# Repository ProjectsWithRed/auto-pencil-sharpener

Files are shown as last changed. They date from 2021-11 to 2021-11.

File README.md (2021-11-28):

# Automatic pencil sharpener

An automatic pencil sharpener machine that works using linear motion. You can sharpen any pencil just by pressing a button and it will take care of the rest, including gathering up all the rubbish into a container.

There is a [video](https://youtu.be/7P9160cqDPM) associated with this repository/project, I highly recommend watching it before using this repo.

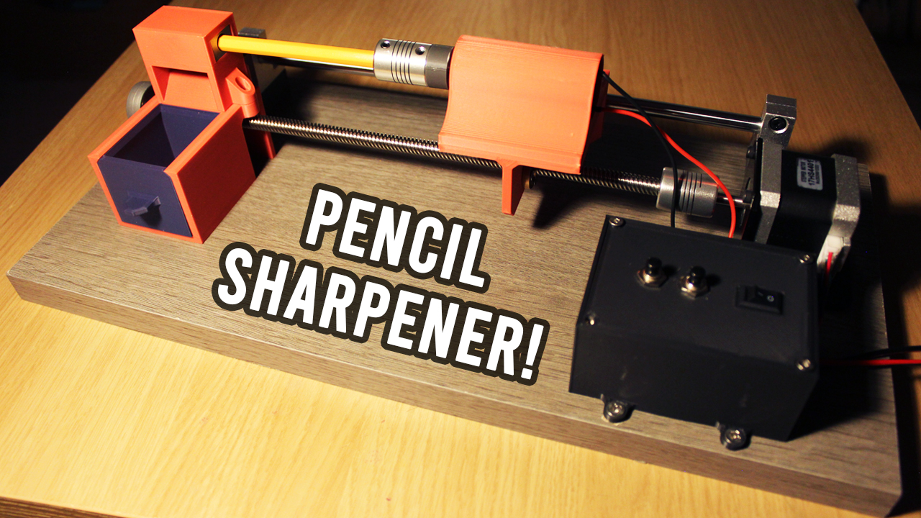
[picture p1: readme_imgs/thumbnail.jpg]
Video (https://youtu.be/7P9160cqDPM "Automatic Pencil Sharpener")


# Arduino

You can find the Arduino sketch in the `auto_pencil_sharpener` directory.

## How to upload code to Attiny MCs if needed

- The Attiny MCs can be programmed just like any Arduino and it's very easy to upload code to them.
- You just need a USBASP adapter, then simply make the connections as shown in the image below.

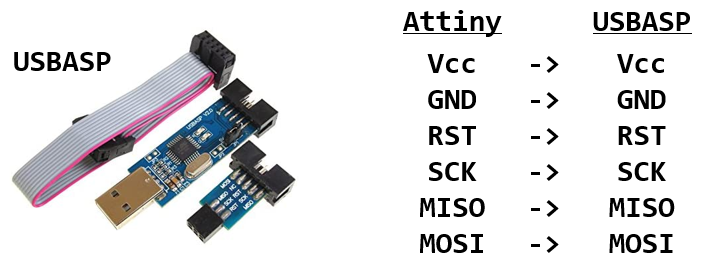
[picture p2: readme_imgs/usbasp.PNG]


- You will also need to install the Attiny boards using the [AttinyCore](https://github.com/SpenceKonde/ATTinyCore) board manager by placing this link `http://drazzy.com/package_drazzy.com_index.json` to your "Additional Boards Manager URLs", which can be accessed in `File > Preferences`.

- From `Tools > Board`, choose your Attiny board with the no bootloader option.
- Then go to `Tools > Programmer` and choose `USBasp (ATTinyCore)`, and then press `Tools > Burn Bootloader`.
- Then to simply upload code, use `Sketch > Upload Using Programmer`.

- You can use stripboards with some wires to make uploading code to the Attiny MCs more convenient:

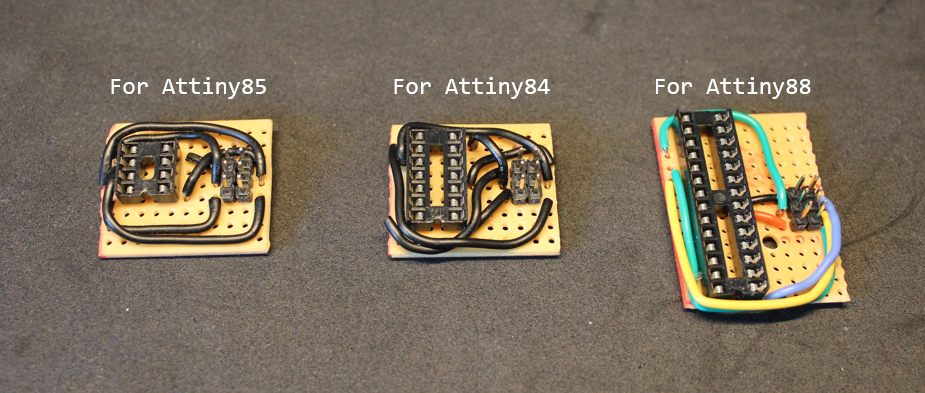
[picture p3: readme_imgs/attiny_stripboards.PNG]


# Components

- `Attiny84`, for the micro-controller.
- `Nema 17` stepper motor, to drive the linear motion.
- `A4988` stepper motor driver, with 100µF-1000µF capacitor across the motor power pins.
- `12V` power supply, with at least 3A max rated current.
- `LM2596` DC-DC step up/down converter, to convert 12V to 5V. 12V is required for the motors, 5V for the micro-controller.
- `MCP1700`, 5V voltage regulator, to ensure the Attiny84 has a consistent and smooth voltage. 1000/100µF and 100,000pF capacitors are soldered directly on the MCP1700 to deal with voltage spikes.
- `12V DC motor`, the one used has a max speed of 500 RPM.
- `IRF3708 MOSFET`, to be able to control the DC motor using a micro-controller.
- `1N4004 Diode`, to be placed across the DC motor to prevent negative voltage spikes if the DC motor is rotated when the circuit is off.
- `Sliding switch`, as an on and off switch.
- `2 buttons`, to control the stepper motor, left and right controls.
- `8mm L30cm lead screw`, for the linear motion.
- `8mm L30cm smooth rod`, for the linear rail for the linear motion.
- `Pillow block bearing`, for the lead screw.
- `SCS8UU linear bearing`, for the smooth rod.
- `SK8 rod support` (x2), for the smooth rod.
- `D19L25 5x8mm flexible shaft coupling` (x2), one to attach lead screw to stepper motor and one to attach pencil to DC motor.

Optional:
- `Potentiometer`, this will be used to fine-tune the speed of the stepper motor, so it does not move too fast towards the sharpener.

# Wiring

## Breadboard

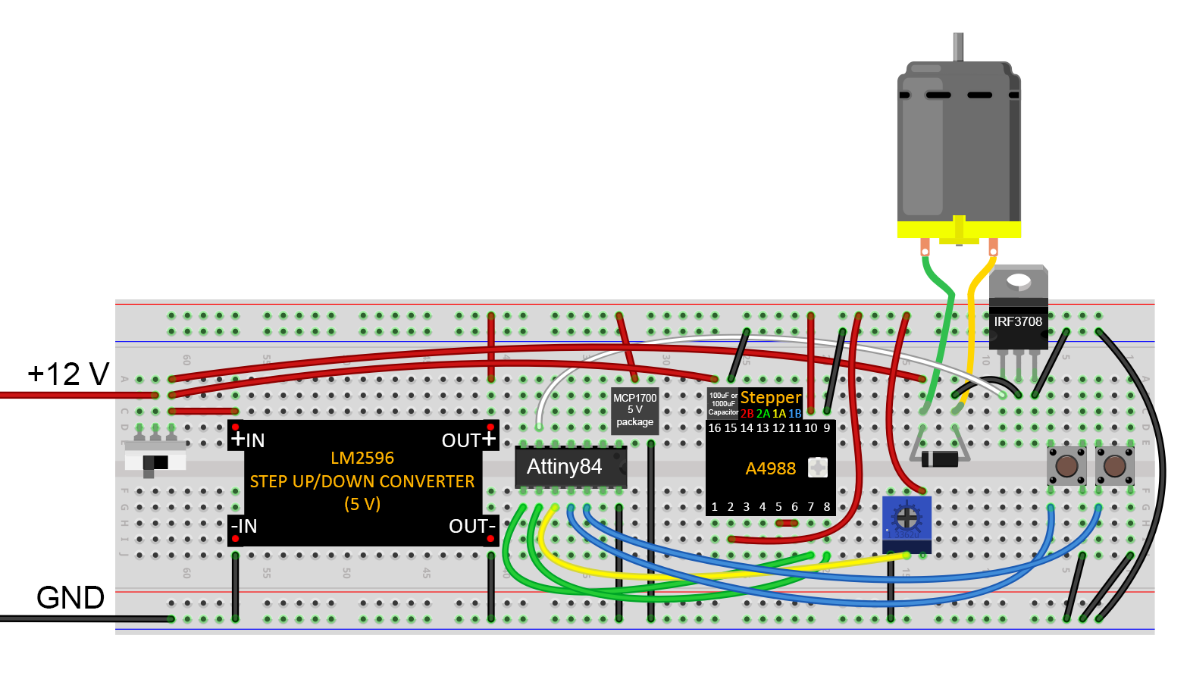
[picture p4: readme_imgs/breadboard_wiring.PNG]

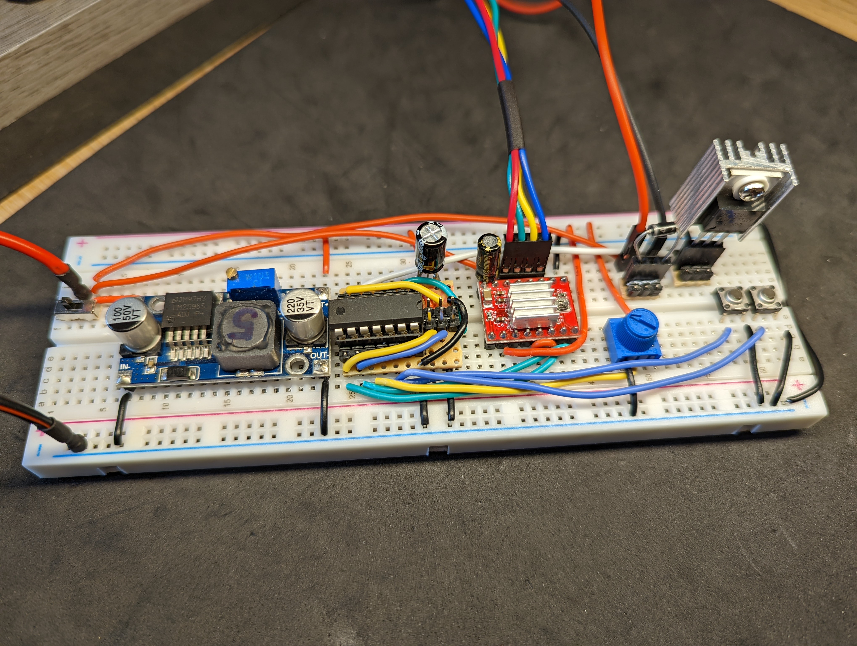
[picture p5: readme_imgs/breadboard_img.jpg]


## Stripboard

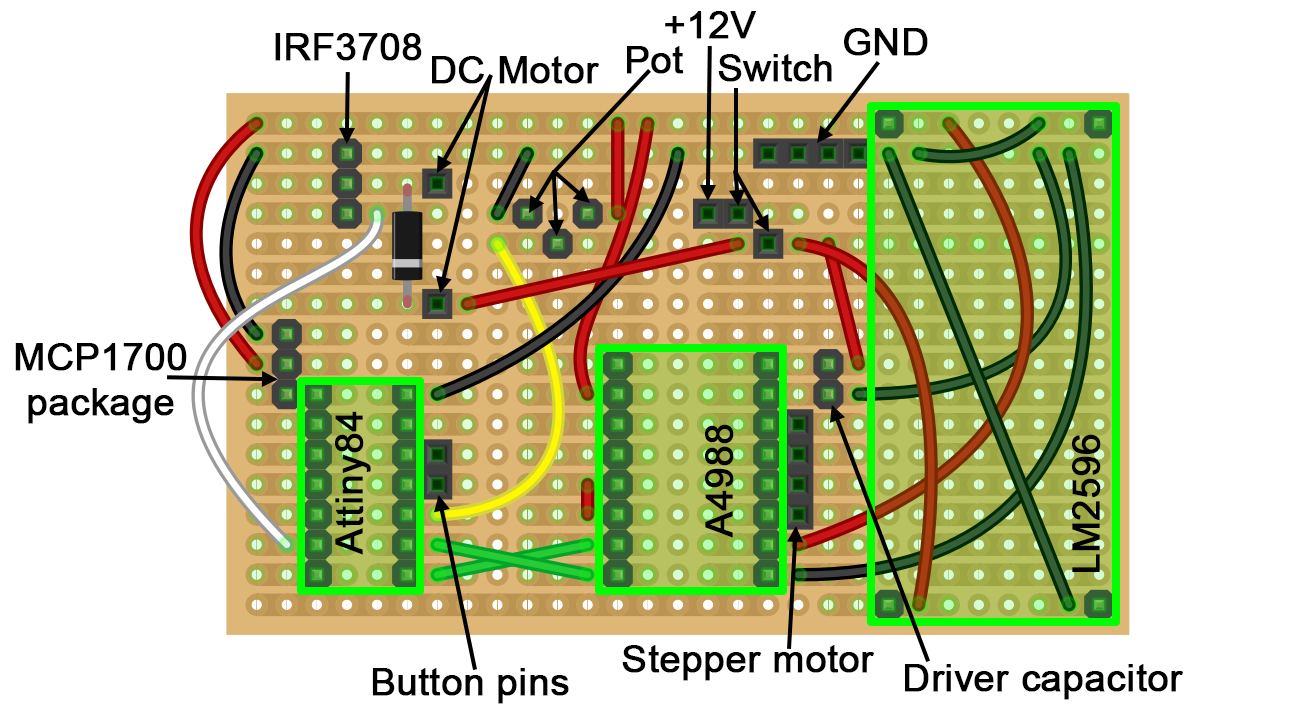
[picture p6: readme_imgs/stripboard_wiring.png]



# 3D printing

Please refer to the `/3d_printing` directory.

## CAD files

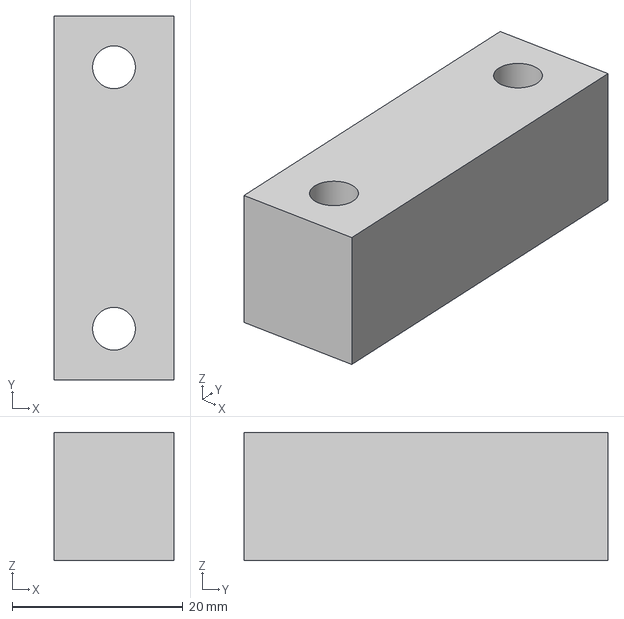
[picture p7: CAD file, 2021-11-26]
3d_printing/smooth_rod_support.3mf
14.0 x 42.6 x 15.0 mm

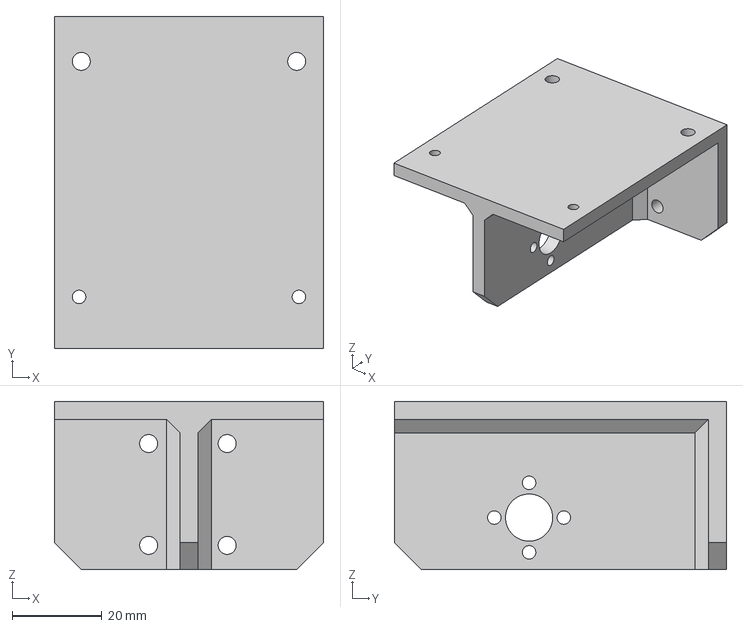
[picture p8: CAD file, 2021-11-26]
3d_printing/dcmotor_platform.3mf
60.0 x 74.0 x 37.5 mm

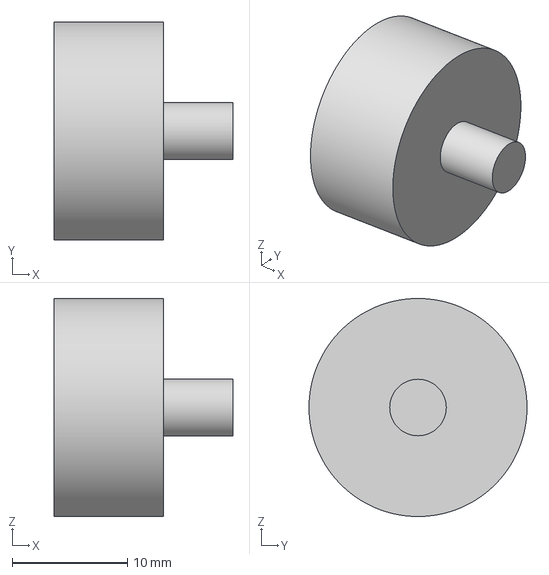
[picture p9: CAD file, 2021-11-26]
3d_printing/dcmotor_coupler.3mf
15.5 x 18.9 x 18.9 mm

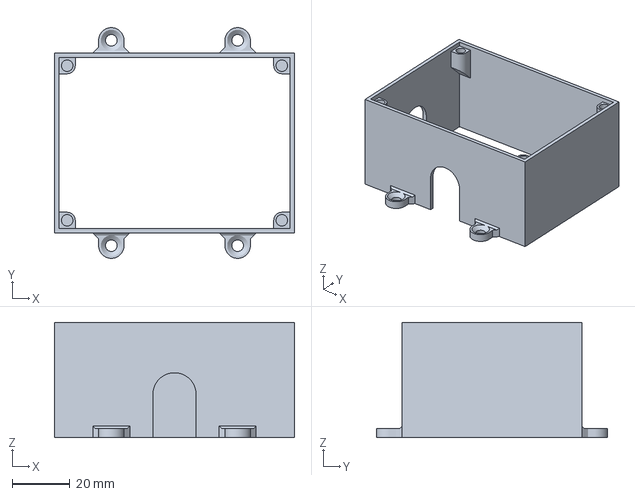
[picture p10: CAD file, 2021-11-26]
3d_printing/wiring_housing.3mf
83.2 x 80.0 x 40.0 mm

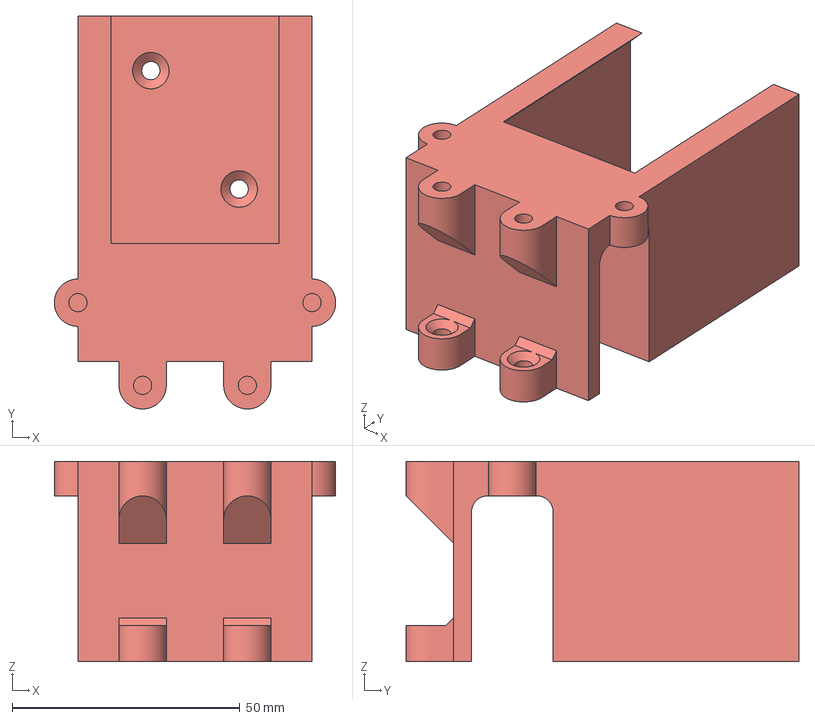
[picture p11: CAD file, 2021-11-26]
3d_printing/sharpener_platform.3mf
61.8 x 86.3 x 44.0 mm

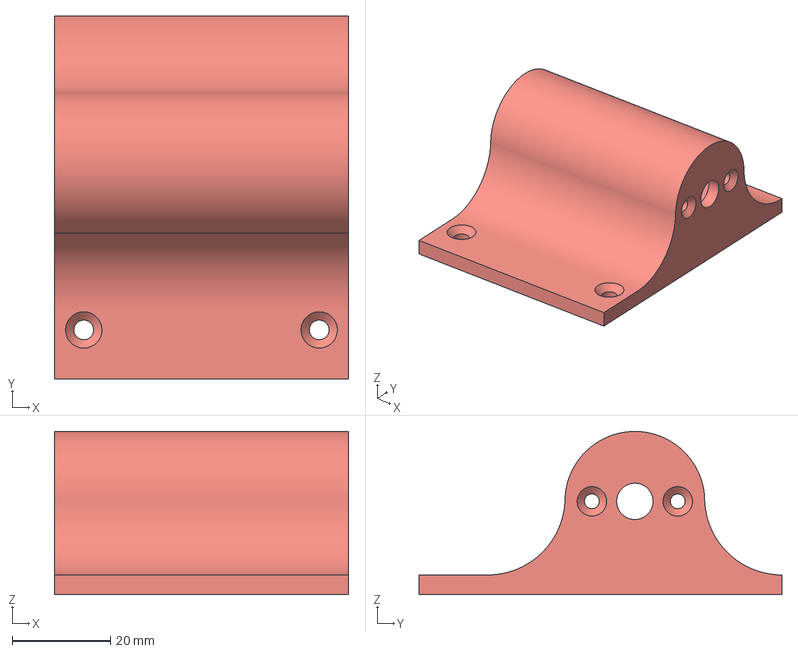
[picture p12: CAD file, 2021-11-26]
3d_printing/dcmotor_housing.3mf
60.0 x 74.0 x 33.3 mm

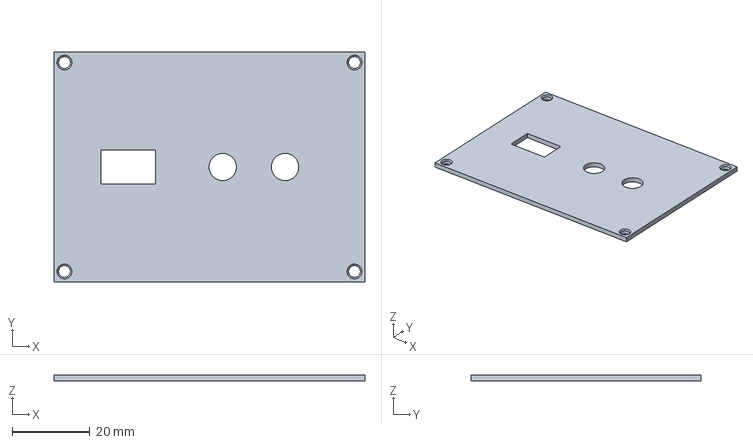
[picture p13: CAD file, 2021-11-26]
3d_printing/wiring_housing_lid.3mf
79.8 x 59.0 x 1.60 mm

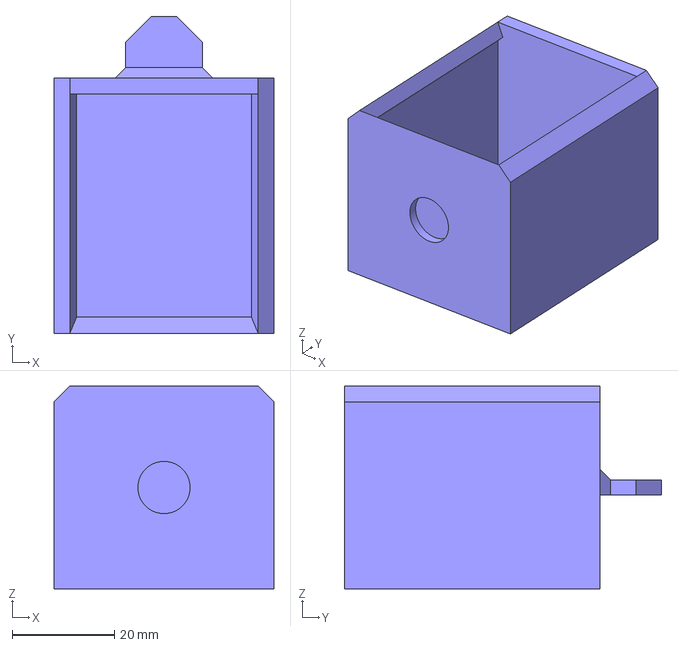
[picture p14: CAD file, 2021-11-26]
3d_printing/container.3mf
43.0 x 62.0 x 39.6 mm

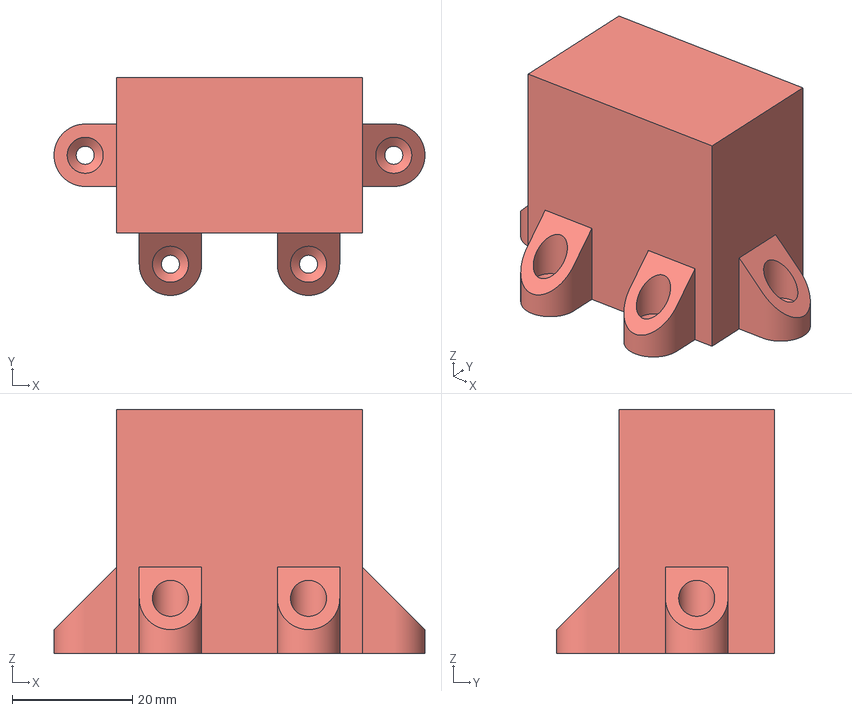
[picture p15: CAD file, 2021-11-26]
3d_printing/sharpener_housing.3mf
61.8 x 36.3 x 40.7 mm

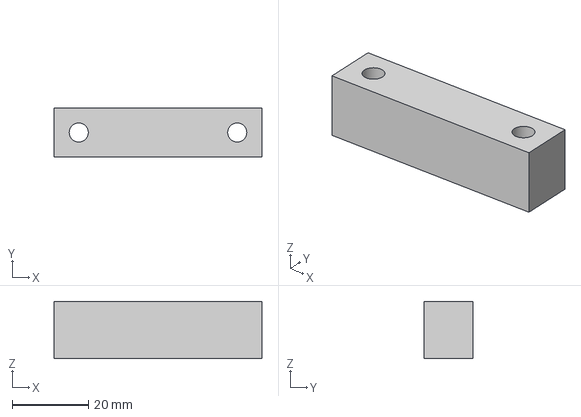
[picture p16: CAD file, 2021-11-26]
3d_printing/lead_screw_support.3mf
54.6 x 12.8 x 15.0 mm

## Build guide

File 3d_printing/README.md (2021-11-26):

# 3D Printing

All the 3D printed parts used in this project.

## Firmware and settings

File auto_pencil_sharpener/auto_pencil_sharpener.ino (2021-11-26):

#include <Stepper.h>

#define motorInterfaceType 1


const int STEPPER_STEP_PIN = 5;
const int STEPPER_DIR_PIN = 4;

const int STEPPER_POT_PIN = A3;  // To control the speed of the stepper motor.

// To control the stepper motor left and right movement.
const int STEPPER_L_BTN_PIN = 2;
const int STEPPER_R_BTN_PIN = 1;

const int STEPPER_STEPS = 1;  // Stepper steps movement at a time.

const int DCMOTOR_MOSFET_PIN = 7;



Stepper stepper(200, STEPPER_DIR_PIN, STEPPER_STEP_PIN);



int stepperSpeed = 200;
int prevStepperSpeed = stepperSpeed;  // Previous stepper speed.

// Current position/step of the stepper motor, where 0 is all the way to the right.
int stepperCurrStep = 0;

// Start and end positions of the stepper motor, this is to ensure that the stepper motor stops before linear rail ends.
int stepperStartSteps = 0;
int stepperEndSteps = -26000;



void setup() {
    stepper.setSpeed(stepperSpeed);

    pinMode(STEPPER_L_BTN_PIN, INPUT_PULLUP);
    pinMode(STEPPER_R_BTN_PIN, INPUT_PULLUP);

    pinMode(DCMOTOR_MOSFET_PIN, OUTPUT);
}


void handleStepper() {
    getStepperSpeed();
    updateStepperSpeed(stepperSpeed);

    int stepperLBtn = digitalRead(STEPPER_L_BTN_PIN);
    int stepperRBtn = digitalRead(STEPPER_R_BTN_PIN);

    if(stepperLBtn == 0 && stepperCurrStep >= stepperEndSteps) {
        stepper.step(-STEPPER_STEPS);
        stepperCurrStep -= STEPPER_STEPS;
        handleDCMotor(1);
    } else if(stepperRBtn == 0 && stepperCurrStep < stepperStartSteps) {        
        stepper.step(STEPPER_STEPS);
        stepperCurrStep += STEPPER_STEPS;
        handleDCMotor(0);
    } else {
        stepper.step(0);
        handleDCMotor(0);
    } 
}


void getStepperSpeed() {
    int stepperPotVal = analogRead(STEPPER_POT_PIN) / 100;
    stepperSpeed = map(stepperPotVal, 0, 10, 50, 2000);
    stepperSpeed = stepperSpeed;
}


void updateStepperSpeed(int newStepperSpeed) {    
    if(newStepperSpeed != prevStepperSpeed) {
        stepper.setSpeed(newStepperSpeed);
        prevStepperSpeed = newStepperSpeed;
    }
}


void handleDCMotor(bool dcMotorSpin) {
    digitalWrite(DCMOTOR_MOSFET_PIN, dcMotorSpin);
}


void loop() {
    handleStepper();
}

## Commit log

2021-11-26 Add instructions and 3d models.
    [container.3mf, dcmotor_coupler.3mf, dcmotor_housing.3mf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]
2021-11-26 Add breadboard wiring.
2021-11-26 Add breadboard image and stripboard wiring/image.
